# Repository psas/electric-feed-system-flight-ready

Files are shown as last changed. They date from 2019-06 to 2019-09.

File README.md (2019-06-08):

# electric-feed-system-flight-ready

## Introduction

The goal of this project was to develop a cryogenic compatible, flight-ready electric feed system (EFS) for Portland State Aerospace Society for use in their upcoming Launch Vehicle 4 (LV4). This project has made significant advancements in the design and testing of a cryogenic compatible pump. However, more work must be completed before the EFS will be deemed flight-ready. Improvements were made upon previous EFS team’s designs, resulting in a more compact, higher powered, and robust pump system. Crucially, the new design has been tested and confirmed to be cryogenic compatible. The final EFS design has successfully shown PSAS that the pump design is capable of pumping cryogenic fluids without seizing and is able to maintain single-phase fluid flow at the system outlet under specified conditions.

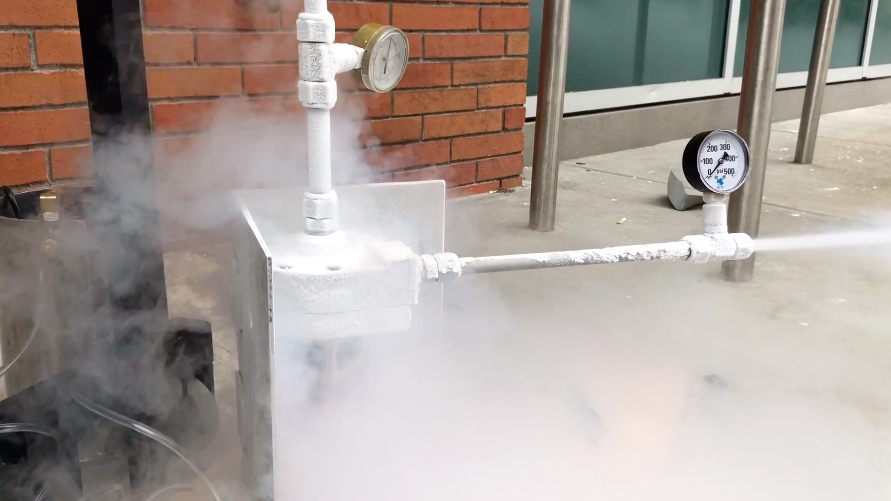
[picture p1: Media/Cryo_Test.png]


## EFS Onboarding

The testing performed on the final cryogenic EFS design for the 2018-2019 PSAS Capstone provided useful knowledge to the organization for continued EFS development. The successful testing of this pump showed that the cryogenic tolerancing functions developed by our team accurately compensate for thermal deformation in the aluminum pump components to allow for proper rotary alignment. Additionally, the cryogenic EFS test showed that this design is capable of pressurizing the cryogenic fluid to obtain single phase fluid flow at the system exit. However, testing has also led to a better understanding of the further work that needs to be performed in order to ready the EFS for flight on LV4. These next steps are outlined below.

### Pump Internals

#### Bearings

The use of a single stainless steel axial thrust roller bearing in the IPA pump displayed inadequate alignment capabilities during this pump's tests. For this reason, the roller bearing was used in conjunction with a Boca ceramic thrust bearing. This resulted in reduced opportunity for misalignment along the rotating element. However, during cryogenic testing, there were several instances of the exit flow momentarily transitioning to gaseous nitrogen at the pump outlet. While the exact cause of this phase duality is not immediately known, one potential source of inconsistency in performance may be from the stainless steel bearing. At cryogenic temperatures, the material of this bearing will contract, which leaves potential for the bearing rollers to rock in the race. For this reason, it is suggested that the second bearing be replaced with either another fully ceramic bearing, or a ceramic-stainless hybrid bearing. This will satisfy the material compatibility of liquid oxygen while ensure optimal performance at cryogenic temperatures.

#### Seals

Testing of the IPA pumps were largely unsuccessful. Misalignment of the rotating element caused the pump to seize during operation. Because the motors selected for the EFS are not rated for high torque applications, this rapid increase in torsional load on the shaft caused the ESC to overload. The likely cause of this was a drastic increase in current as the motor attempted to rotate the pump shaft.

The Flowserve PacSeal used for IPA testing is believed to be, at least in part, the reason for this misalignment. The seal is designed be able to move along the shaft as needed to account for the increase in volute pressure. However, the seal did not perform as designed during testing, and the shaft locked in place.

Additionally, the seal did not adequately retain the fluid as intended. This seal was ultimately selected as a placeholder in the first place, due to it's low cost and ease of accessibility. However, the specifications of this seal do not meet the requirements of the electric feed system in the first place, and as such should not be used in future designs.

For cryogenic testing, the EFS team had to find a sealing solution to meet the upcoming deadline for cryogenic testing. For this reason, a PTFE press-fit sealing collar was developed as a temporary sealing solution. It performed well enough for the purposes of this cryogenic test. However, during this test, gaseous nitrogen leaked from the sealing chamber. For this reason, it is not recommended that this design be considered for future EFS iterations.

Research performed regarding cryogenic dynamic seals with LOX compatibility has led to the selection of a Parker FCC-V spring energized seal (or an equivalent seal from Gallagher Seals) as the optimal seal for both IPA and LOX applications. This selection was identified before cryogenic testing took place. However, due lack of easy access to this seal type, the EFS team was not able to procure seals in time for testing. In the future, it is advised that the next EFS team work on obtaining these seals early on in the development stage.

In order to reduce the total pressure on the seal, it is recommended that the impeller be optimally balanced by adding shallow Barske vanes on the rear face of the impeller in addition to the suction vanes. This helps influence the fluid away from the sealing chamber and back out toward the diffuser, reducing the total pressure the seal experiences.

### Rotary Element Alignment

The sealing and bearing solutions outlined above will help improve alignment in pump shaft rotation. Additionally, a direct motor mount was developed to further decrease variation in alignment. This design improved alignment during cryogenic testing, and is advised to be used in all future designs.

Additionally, it is recommended that the next EFS team consider procuring a motor with an custom extended shaft. With enough length, this shaft can be used to drive the pump directly, removing the need for a coupler. This would reduce the overall size of the system and further improve alignment.

### Instrumentation

While testing of the cryogenic pump was successful and provided results that benefited the development of the PSAS electric feed system, the analog pressure gauges used during the test were not able to operate at such low temperatures. Because of this, no quantitative results were obtained from the test.

Moving forward, it is recommended that further research is performed into cryogenic compatible pressure and flow rate instruments. Ideally, pressure transducers should be integrated into the DAQ system to allow digital conversion of the data. The PSAS Liquid Fuel Engine Test Stand (LFETS) team has performed reasonable amounts of research into both of these instrument types, and their work can be used as a resource for how these measurement devices can best be integrated into the EFS. A LOX compatible differential pressure flowmeter (Venturimeter) is recommended for mass flow data collection. 

### LV4 Integration

#### Test Stand

Future iterations of the EFS pumps should be capable of integrating into the LFETS and used to regulate the pressure and mass flow delivered to the test engine. Once on the test stand, the flow rate and pressure measurements discussed previously will already be measured by the test stand's instrumentation. In this way, both projects will benefit from the work of the other.

#### LV4 Airframe

The current mounting design for both electric feed system pumps consists of the 2 pumps encased in a rectagular mount on opposite corners. This configuration was designed to be compatible with the 12 inch diameter selected for LV4. However, it will be the responsibility of future EFS teams to identify and test the best way to integrate these mounts into the rocket module itself.

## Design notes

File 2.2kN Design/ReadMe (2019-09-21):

Contains calculation tools and Solidworks parts and assemblies for IPA and LOX EFS pumps for use in the 2.2kN LV4 engine.

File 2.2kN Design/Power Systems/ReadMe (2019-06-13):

Block diagrams for EFS overall system and power configuration.

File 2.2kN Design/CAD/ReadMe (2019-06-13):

Solidworks assemblies and parts for IPA and LOX pumps are found in this directory.

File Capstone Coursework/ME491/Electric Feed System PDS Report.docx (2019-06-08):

Product Design Specifications Report

# Flight Ready Electric Feed System

Portland State University

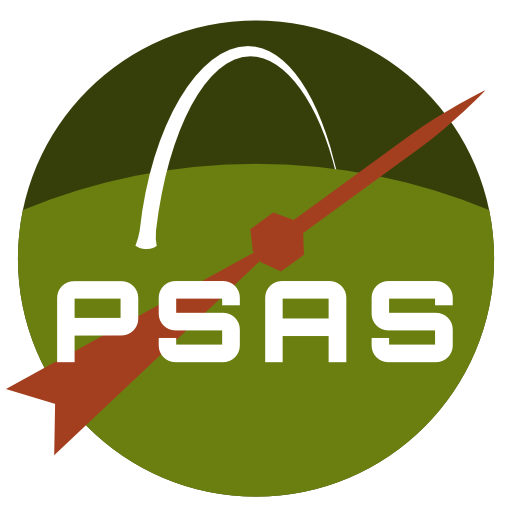
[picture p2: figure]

Group members:

Elrod, Shayli

Garcia, Julio

Ju, Henry

Mendoza, Jonas

Sheldon, Nick

Wahl, Philip

Academic Advisor: Baldur Steingrimsson

Sponsor: Portland State Aerospace Society

DOCUMENT CONTENTS

INTRODUCTION 2

MISSION STATEMENT 2

PROJECT PLAN (Top-Level) 3

CUSTOMER IDENTIFICATION 5

CUSTOMER FEEDBACK 5

PDS 6

CONCLUSIONS 8

ATTACHMENTS 8

### INTRODUCTION

Portland State Aerospace Society (PSAS) requires the production of a device that can be used to increase fluid pressures in both the Liquid Fuel Engine Test Stand (LFETS) and PSAS liquid fuel rockets in flight. The Flight Ready Electric Feed System (EFS) is an electronically controlled pump system to be designed for the Launch Vehicle 4 (LV4). This project has been proposed by PSAS in order to make the use of lightweight, low-pressure composite propellent flight tanks possible. As opposed to utilizing a more traditional high pressure 'blow down" system, an EFS will be used to provide the necessary pressure to pump the propellants into the engine. Design and manufacturing of the EFS will be a part of a senior capstone project involving six Mechanical Engineering students. This approachable and affordable alternative to a pressurized tank is a challenging and innovative task for an amateur rocket design.

### MISSION STATEMENT

“To provide affordable, lightweight propulsion system technology increasing the capabilities of amatuer rocketry and student education.”

### PROJECT PLAN (Top-Level)

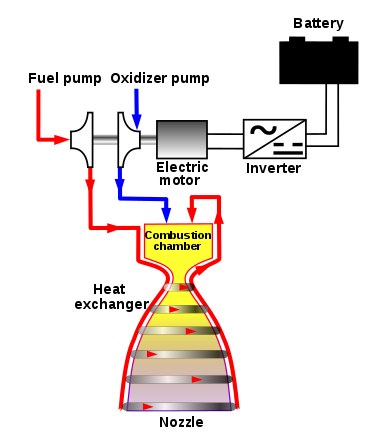
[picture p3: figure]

The pump design will utilize electric drive shafts to introduce mechanical work into the system in order to produce a pressure increase. Each housing will be optimized for the required pressure of two independent fluids. The pump design will be optimized for flight capability, utilizing a compact lightweight casing to enclose individual chambers which separately increase the pressure of Isopropyl Alcohol and Liquid Oxygen. The pump will be powered by an onboard Lithium Ion battery pack, providing DC current to an electric inverter. AC converted current will power the brushless motors to provide shaft power in order to rotate off the impellers within the system. As the system provides rotational energy, the pressure of the incoming propellants will increase from 45 PSI to 500 PSI as the impellers increase the propellant potential energy.

The manufacturing process will begin with 3D rendering in SolidWorks to create the shape and layout of the housings and motors. A machinable prototype needs to fit within specified dimensions of the airframe module which will house the onboard EFS. A functional design will be followed by ANSYS vibrational and thermal analysis to show evidence of structural integrity. Once the design has been analytically verified, it will be approved and passed on to the CNC machine shop for physical fabrication. Initial machine prototypes will be machined out of inexpensive plastics for trial mock-ups before any machining out of metal will begin.

The corrosive properties of liquid oxygen will limit the material options for pump component which will come into contact with it. 304 Stainless steel is the most common metal alloy used for liquid oxygen components, and its availability makes it a logical candidate for material selection. In addition, research will be performed on the feasibility of using alternative materials that may be more cost effective and easier to machine, such as aluminum alloys.

Tolerance testing will begin upon completion of machined parts in either plastic or metal. All dimensions will be compared against the CAD model for machining accuracy and precision. Once a metal casing has been created leak testing will check for fitment of the final assembly. The pump will be assembled and then filled with water, up to 1000 psi, to search for any leaks in the system. Continued system testing will research durability against vibrational and acceleration force as the pump will be subjected to a harsh launch environment. It is imperative that the system is not compromised so the rocket can achieve consistent thrust during flight.

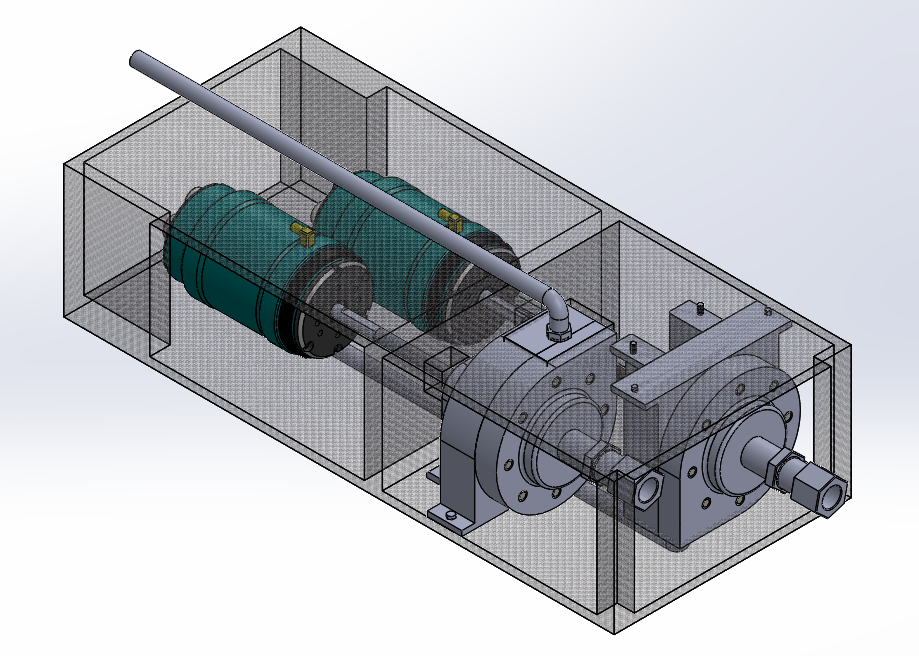
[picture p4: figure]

Upon completion, the desired deliverable is a tested electronically controlled pump that is suitable for successful use during flight. Crucially, the pump and associated system components must be compatible both propellants and ensure absolute fluid separation at all points within the system. Cross-contamination of fluids will be considered a design failure and impose a major safety risk. The minimum lifespan without significant overhaul is ten full-length engine test fires. Surpassing ten fires is preferred if at all possible. The pump and its related systems should be embedded with sensors for required data collection, as this testing data is also a deliverable. The milestone timeline for the project can be seen in Table 2 (see attachments).

### CUSTOMER IDENTIFICATION

Portland State Aerospace Society will be sponsoring this capstone project and is responsible for all the given requirements. In addition, the Oregon NASA Space Grant Consortium (OSGC) will also be sponsoring our Flight Ready EFS capstone after winning an Undergraduate Team Experience Award Program grant. This additional sponsor will add extra requirements to be fulfilled by the capstone team such as a project presentation to the OSGC board as publishing project documentation. The requirements from both customers are outlined in Table 3 (see attachments).

### CUSTOMER FEEDBACK

The Flight Ready EFS Capstone group will provide a weekly update to PSAS through a short presentation at the general meetings. This will ensure all progress is shared with the customer and all designs are to be to review as they progress. Use of funds will involve direct communication with OSGC on a per part basis. All purchase requests will be review by the team’s Principal Investigator and then sent off to OSGC for reimbursement. All declined part requests will undergo a secondary review in order to reselect a similar part which can be purchased.

### PRODUCT DESIGN SPECIFICATION (PDS)

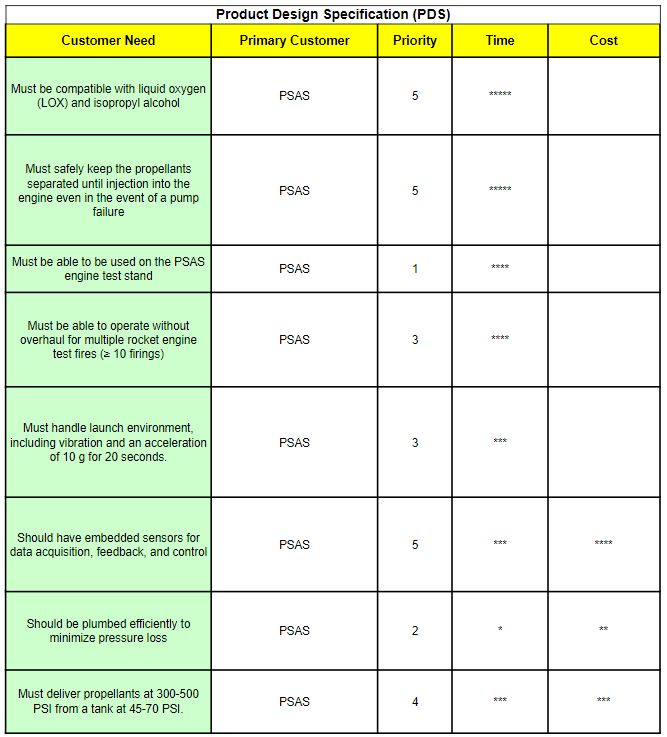
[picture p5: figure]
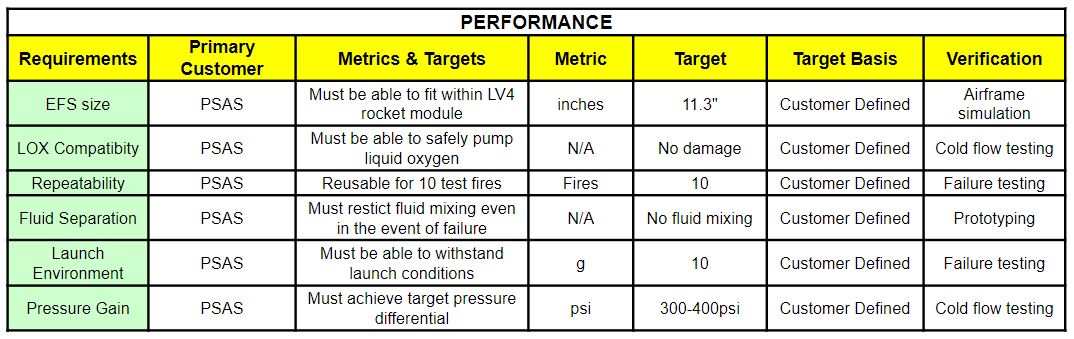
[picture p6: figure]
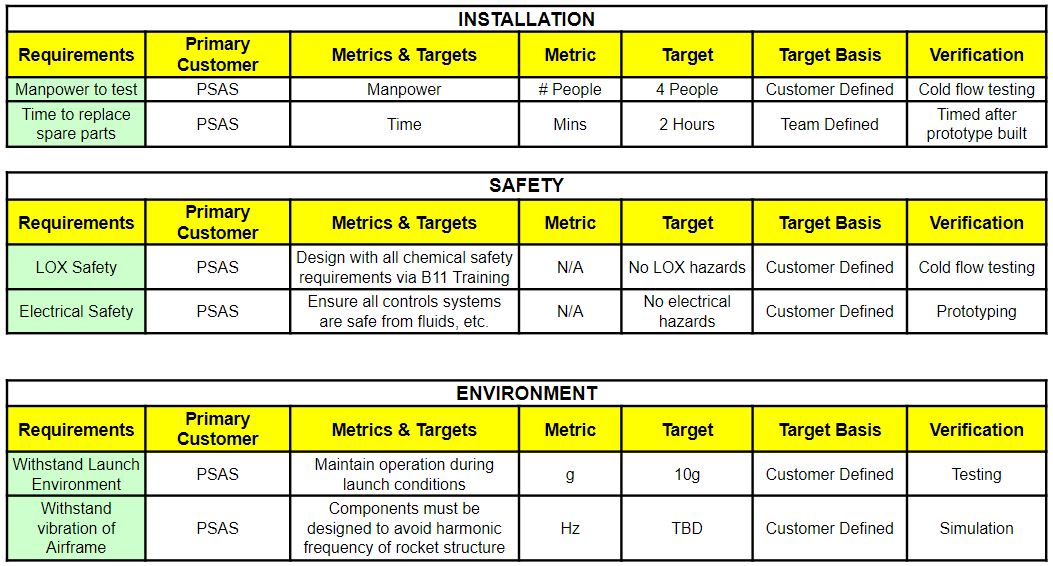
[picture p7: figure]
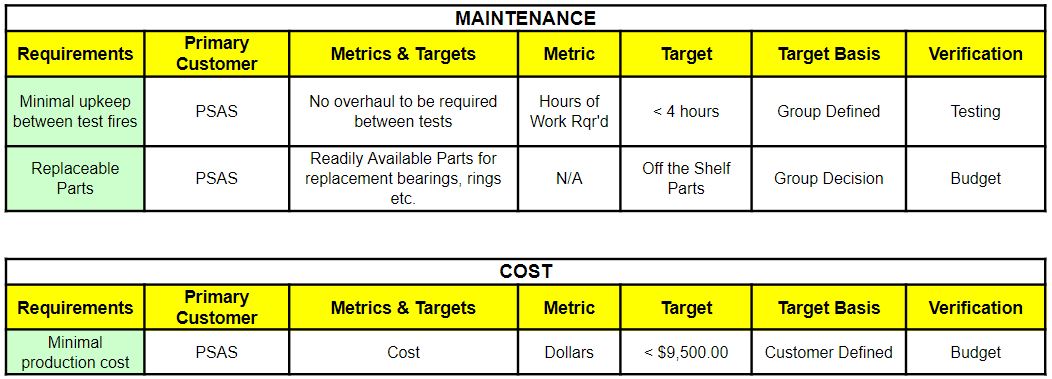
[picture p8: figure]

### CONCLUSIONS

The Flight Ready Electric Feed System, upon completion, will be a major accomplishment for the amateur aerospace community. This project will further develop research performed by previous and concurrent PSU Capstone teams associated with the liquid propulsion team within PSAS. Over the next few months, we anticipate developing a cryogenic, electronically controlled, propellant delivery system for Launch Vehicle 4 as specified by our Capstone Sponsor, PSAS. By the end of the school year will be presenting our findings, prototype, and publish all documentation related to the project.

### ATTACHMENTS

Table 1: Electric Feed System Project Budget

Item | Description | Vendor | Award Amount | 1.5:1 Cost Share

Cost Share
In-Kind AY effort | Dr. Mark Weislogel donating his time working as PI on Project | Portland State University | | $6,556

Award Budget
304 SS Steel | The raw material used to machine pump housing | McMaster-Carr | $800
Tooling | Pump House machine tooling | Western Precision Products Inc | $1,400
6061 Aluminum | Raw Material to create EFS Airframe Structure | McMaster-Carr | $200
304 SS Steel | ¼” x 24” TGP Precision Shaft | Metals Depot | $10
Impeller | Rotational Impellers for propellants | Shapeways | $200
ISO Plumbing | Various plumbing fittings for alcohol | Home Depot | $100
LOX Plumbing | Various LOX compatible fittings | AcmeCryo | $300
Aluminum Piping | ½” Aluminum piping for plumbing | Metals Depot | $100
Seals | Metal C-Ring Internal Pressure Face Seals | Parker | $30
Liquid Oxygen | 40 Gallons of LOX for testing | Airgas | $200
Liquid Nitrogen | 40 Gallons of LN for cryo testing | Airgas | $200
Electric Motor | Brushless Motor for shaft drive | Hobbyking | $150
Heat Sink | Heat Sink for Brushless motor | Amazon | $25
Arduino | Arduino to Controlling pump | Amazon | $50
Sensing Equipment | Pressure Transducers and flow meters for fluid monitoring | Omega | $500
Total Direct Costs | | | $4,265 | $6,556
Total Indirect Costs | | 48.50% | $2,069 | $3,180
Total Project Costs | | | $6,334 | $9,736
Cost Share Ratio | 1.537

Table 2: EFS Completion Timeline

Week | Milestone Description
1 - 3 | Research and locate budget line items to optimize spending. Discus pump design process to dictate the purchase sequence.
4 - 6 | Finalize design for preliminary prototyping with 3D printing and mock testing
7 - 10 | Integrate Control system with proven test design
11 - 15 | Coordinate Electric Feed System design with Engine Test Stand and Airframe
16 - 20 | Begin manufacturing process for steel housing, plumbing, and airframe fixture
21 - 22 | Testing cryogenic compatibility, fluid leak, and durability to cycle usage
23 - 25 | Department testing with Test Stand and Airframe
26 - 27 | Finalize Electric Feed System Design
28 - 30 | Organize project material for finalized report and presentation

Table 3: Customer Requirements for PSAS and OSGC

PSAS Requirements | NASA OSGC Requirements
Must be compatible with liquid oxygen (LOX) and isopropyl alcohol | Citation of OSGC as a source of funding in all publications
Must safely keep the propellants separated until injection into the engine even in the event of a pump failure | Complete list of resulting publications
Must be able to be used on the PSAS engine test stand | Final budget
Must be able to operate without overhaul for multiple rocket engine test fires (≥ 10 firings) | Report on project outcome
Must handle the launch environment, including vibration and an acceleration of 10 g for 20 seconds. | Presentation of results at the OSGC Student Symposium in (Nov 2019)
Should have embedded sensors for data acquisition, feedback, and control
Should be plumbed efficiently to minimize pressure loss
Must deliver propellants at 300-500 PSI from a tank at 45-70 PSI.

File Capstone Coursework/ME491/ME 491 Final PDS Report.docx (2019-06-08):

ME 491 | Fall 2018

Product Design Specifications Report

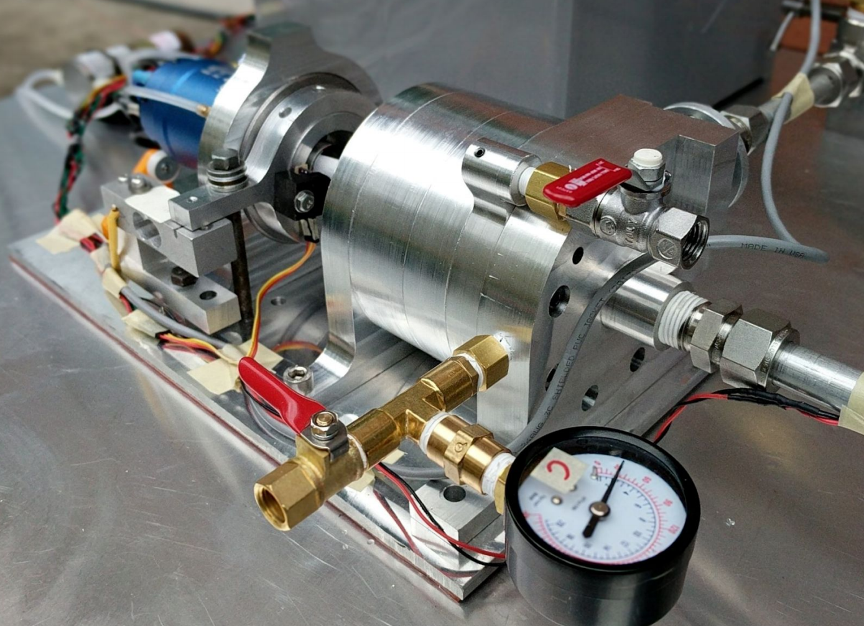
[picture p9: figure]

Flight Ready

Electric Feed System

TEAM MEMBERS:

Julio Garcia

Philip Wahl

Jonas Mendoza

Nick Sheldon

Henry Ju

Shayli Elrod

ACADEMIC ADVISOR:

Baldur Steingrimsson

Sponsored by Portland State Aerospace Society (PSAS)

DOCUMENT CONTENTS

INTRODUCTION 3 (https://docs.google.com/document/d/1pQuV71Iw2FOw1OESzgzDGfmaMRiZPIVxerrv7SGsqSI/edit)

MISSION STATEMENT 3 (https://docs.google.com/document/d/1pQuV71Iw2FOw1OESzgzDGfmaMRiZPIVxerrv7SGsqSI/edit)

PROJECT PLAN (Top-Level) 4-5 (https://docs.google.com/document/d/1pQuV71Iw2FOw1OESzgzDGfmaMRiZPIVxerrv7SGsqSI/edit)

CUSTOMER IDENTIFICATION (https://docs.google.com/document/d/1pQuV71Iw2FOw1OESzgzDGfmaMRiZPIVxerrv7SGsqSI/edit) 6

CUSTOMER FEEDBACK (https://docs.google.com/document/d/1pQuV71Iw2FOw1OESzgzDGfmaMRiZPIVxerrv7SGsqSI/edit) 6

PDS (https://docs.google.com/document/d/1pQuV71Iw2FOw1OESzgzDGfmaMRiZPIVxerrv7SGsqSI/edit) 7-8

CONCLUSIONS (https://docs.google.com/document/d/1pQuV71Iw2FOw1OESzgzDGfmaMRiZPIVxerrv7SGsqSI/edit) 9

ATTACHMENTS (https://docs.google.com/document/d/1pQuV71Iw2FOw1OESzgzDGfmaMRiZPIVxerrv7SGsqSI/edit) 10-12

INTRODUCTION

Portland State Aerospace Society (PSAS) requires the production of a flight ready device that can be used to increase fluid pressure in both the Liquid Fuel Engine Test Stand (LFETS) and PSAS liquid fuel rocket. The Flight Ready Electric Feed System (EFS) is an electronically controlled pump system to be designed for the Launch Vehicle 4 (LV4). This project has been proposed by PSAS in order to make the use of lightweight, low-pressure, composite propellent flight tanks possible. As opposed to utilizing a more traditional high pressure 'blow down" system, an EFS will be used to provide the necessary pressure to pump the propellants into the engine. Design and manufacturing of the EFS will be a part of a senior capstone project involving six Mechanical Engineering students. This approachable and affordable alternative to a pressurized tank is a challenging and innovative task for an amateur rocket design.

MISSION STATEMENT

“To provide an affordable, lightweight propulsion system technology increasing the capabilities of amateur rocketry and student education.”

PROJECT PLAN (Top-Level)

The pump design will utilize electric drive shafts to introduce mechanical work into the system in order to produce an increase in pressure. Each housing will be optimized for the required pressure of two independent fluids. The pump design will be designed for flight capability, utilizing a compact lightweight casing to enclose individual chambers which separately increase the pressure of isopropyl alcohol and liquid oxygen (Figure 1). The pump will be powered by an onboard lithium ion battery pack, providing DC current to an electric inverter. AC converted current will power the brushless motors to provide shaft power in order to rotate off the impellers within the system. As the system provides rotational energy, the pressure of the incoming propellants will increase from 45 PSI to 500 PSI as the impellers increase the propellant potential energy.

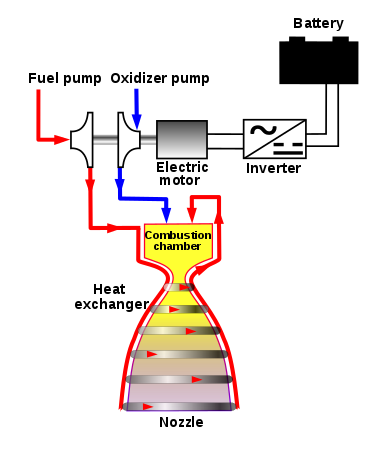
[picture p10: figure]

Figure : Overview of EFS System

The manufacturing process will begin with 3D rendering in SolidWorks to create the shape and layout of the housing and motors. A machinable prototype needs to fit within specified dimensions of the airframe module which will house the onboard EFS. A functional design will be followed by ANSYS vibrational and thermal analysis to show evidence of structural integrity. Once the design has been analytically verified, it will be approved and passed on to the CNC machine shop for physical fabrication. Initial machine prototypes will be machined out of inexpensive plastics for trial mock-ups before any machining out of metal will begin.

The corrosive properties of liquid oxygen will limit the material options available for pump components that will come into contact with it. 304 stainless steel is the most common metal alloy used for liquid oxygen components and its availability makes it a logical candidate for material selection. In addition, research will be performed on the feasibility of using alternative materials that may be more cost effective and easier to machine, such as aluminum alloys.

Tolerance testing will begin upon completion of machined parts in either plastic or metal. All dimensions will be compared against the CAD model for machining accuracy and precision. Once a metal casing has been created leak testing will check for fitment of the final assembly. The pump will be assembled and then filled with water (up to 1000 psi) to search for any leaks in the system. Continued system testing will research durability against vibrational and acceleration force as the pump will be subjected to a harsh launch environment. It is imperative that the system is not compromised so the rocket can achieve consistent thrust during flight.

Upon completion, the desired deliverable is a tested electronically controlled pump that is suitable for successful use during flight. Crucially, the pump and associated system components must be compatible with both propellants and ensure absolute fluid separation at all points within the system. Cross-contamination of fluids will be considered a design failure and impose a major safety risk. The minimum lifespan without significant overhaul is ten full-length engine test fires. Surpassing ten fires is preferred if possible. The pump and its related systems should be embedded with sensors as this testing data is also a required deliverable. The milestone timeline for the project can be seen in Table 2 (see attachments).

CUSTOMER IDENTIFICATION

Portland State Aerospace Society will be sponsoring this capstone project and is responsible for all the given requirements. In addition, the Oregon NASA Space Grant Consortium (OSGC) will also be sponsoring our Flight Ready EFS capstone after winning an Undergraduate Team Experience Award Program grant. This additional sponsor will add extra requirements to be fulfilled by the capstone team such as a project presentation to the OSGC board as publishing project documentation. The requirements from both customers are outlined in Table 3 (see attachments).

CUSTOMER FEEDBACK

The Flight Ready EFS Capstone group will provide a weekly update to PSAS through a short presentation at the general meetings. This will ensure all progress is shared with the customer and all designs are to be to review as they progress. Use of funds will involve direct communication with OSGC on a per part basis. All purchase requests will be review by the team’s Principal Investigator and then sent off to OSGC for reimbursement. All declined part requests will undergo a secondary review in order to reselect a similar part which can be purchased.

PRODUCT DESIGN SPECIFICATION (PDS)

Table 1: Customer Requirements

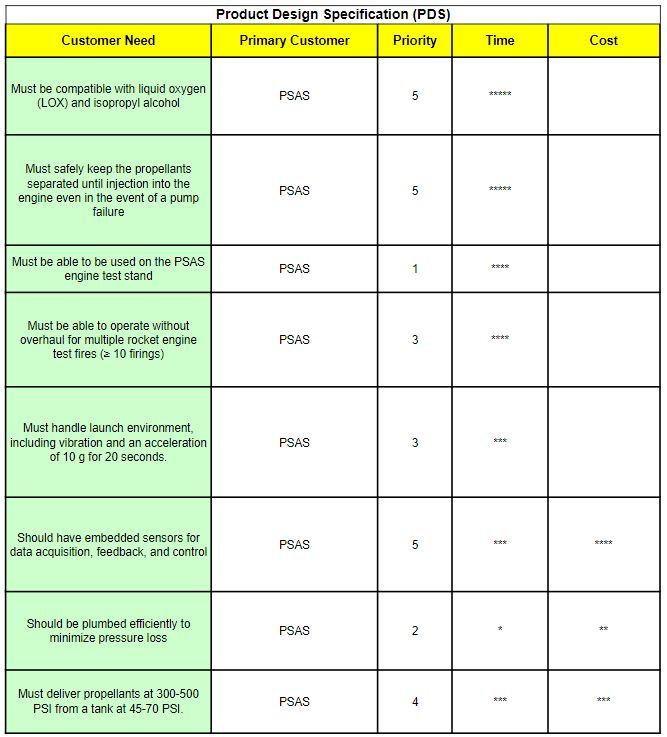
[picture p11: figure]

PRODUCT DESIGN SPECIFICATION (PDS)

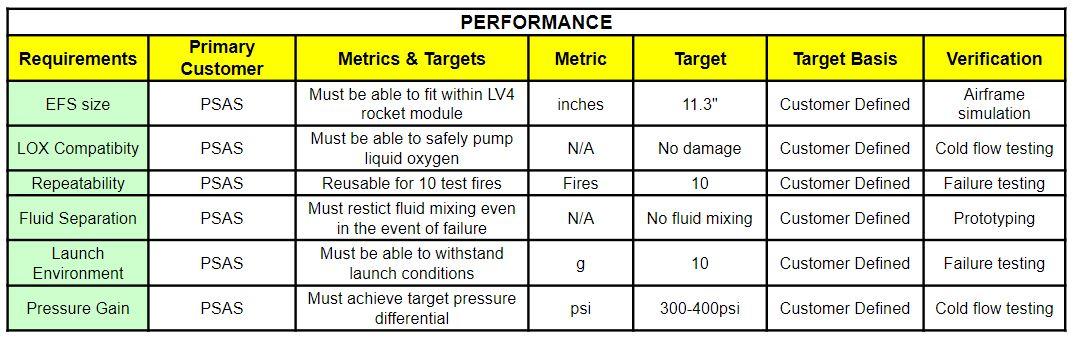
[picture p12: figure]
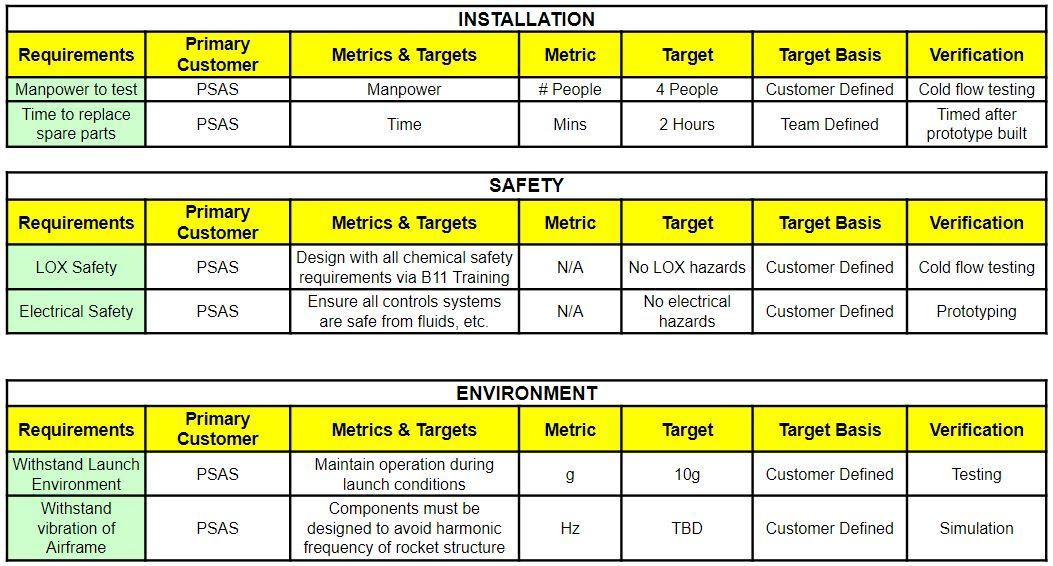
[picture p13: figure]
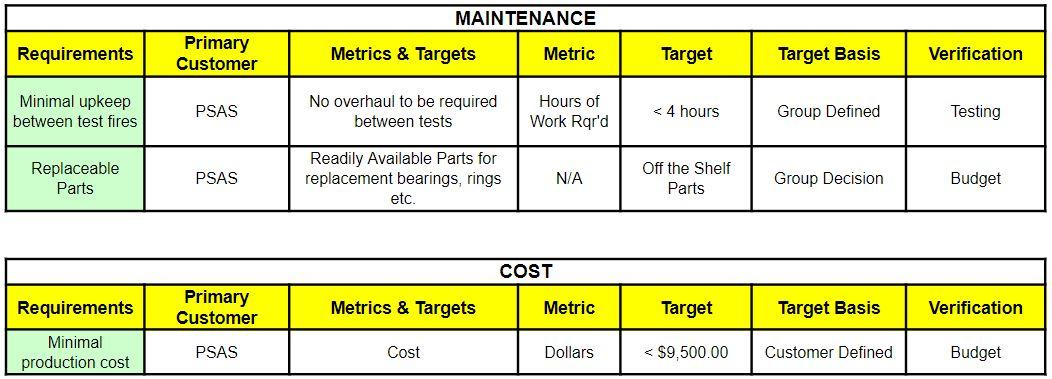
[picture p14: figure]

CONCLUSIONS

The Flight Ready Electric Feed System upon completion, will be a major accomplishment for the amateur aerospace community. This project will further develop research performed by previous and concurrent PSU Capstone teams associated with the liquid propulsion team within PSAS. Over the next few months, we anticipate developing a cryogenic, electronically controlled, propellant delivery system for Launch Vehicle 4 as specified by our Capstone Sponsor, PSAS. By the end of the school year, we will be presenting our findings, prototype, and will publish all documentation related to the project.

ATTACHMENTS

Table 1: Electric Feed System Project Budget

Item | Description | Vendor | Award Amount | 1.5:1 Cost Share

Cost Share
In-Kind AY effort | Dr. Mark Weislogel donating his time working as PI on Project | Portland State University | | $6,556

Award Budget
304 SS Steel | The raw material used to machine pump housing | McMaster-Carr | $800
Tooling | Pump House machine tooling | Western Precision Products Inc | $1,400
6061 Aluminum | Raw Material to create EFS Airframe Structure | McMaster-Carr | $200
304 SS Steel | ¼” x 24” TGP Precision Shaft | Metals Depot | $10
Impeller | Rotational Impellers for propellants | Shapeways | $200
ISO Plumbing | Various plumbing fittings for alcohol | Home Depot | $100
LOX Plumbing | Various LOX compatible fittings | AcmeCryo | $300
Aluminum Piping | ½” Aluminum piping for plumbing | Metals Depot | $100
Seals | Metal C-Ring Internal Pressure Face Seals | Parker | $30
Liquid Oxygen | 40 Gallons of LOX for testing | Airgas | $200
Liquid Nitrogen | 40 Gallons of LN for cryo testing | Airgas | $200
Electric Motor | Brushless Motor for shaft drive | Hobbyking | $150
Heat Sink | Heat Sink for Brushless motor | Amazon | $25
Arduino | Arduino to Controlling pump | Amazon | $50
Sensing Equipment | Pressure Transducers and flow meters for fluid monitoring | Omega | $500
Total Direct Costs | | | $4,265 | $6,556
Total Indirect Costs | | 48.50% | $2,069 | $3,180
Total Project Costs | | | $6,334 | $9,736
Cost Share Ratio | 1.537

Table 2: EFS Completion Timeline

Week | Milestone Description
1 - 3 | Research and locate budget line items to optimize spending. Discus pump design process to dictate the purchase sequence.
4 - 6 | Finalize design for preliminary prototyping with 3D printing and mock testing
7 - 10 | Integrate Control system with proven test design
11 - 15 | Coordinate Electric Feed System design with Engine Test Stand and Airframe
16 - 20 | Begin manufacturing process for steel housing, plumbing, and airframe fixture
21 - 22 | Testing cryogenic compatibility, fluid leak, and durability to cycle usage
23 - 25 | Department testing with Test Stand and Airframe
26 - 27 | Finalize Electric Feed System Design
28 - 30 | Organize project material for finalized report and presentation

Table 3: Customer Requirements for PSAS and OSGC

PSAS Requirements | NASA OSGC Requirements
Must be compatible with liquid oxygen (LOX) and isopropyl alcohol | Citation of OSGC as a source of funding in all publications
Must safely keep the propellants separated until injection into the engine even in the event of a pump failure | Complete list of resulting publications
Must be able to be used on the PSAS engine test stand | Final budget
Must be able to operate without overhaul for multiple rocket engine test fires (≥ 10 firings) | Report on project outcome
Must handle the launch environment, including vibration and an acceleration of 10 g for 20 seconds. | Presentation of results at the OSGC Student Symposium in (Nov 2019)
Should have embedded sensors for data acquisition, feedback, and control
Should be plumbed efficiently to minimize pressure loss
Must deliver propellants at 300-500 PSI from a tank at 45-70 PSI.

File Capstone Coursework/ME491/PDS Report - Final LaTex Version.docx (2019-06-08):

ME 491 | Fall 2018 Product Design Specifications Report

TO

CHILLE PUS

Flight Ready Electric Feed System

TEAM MEMBERS: Julio Garcia Philip Wahl Jonas Mendoza Nick Sheldon Henry Ju Shayli Elrod

Sponsored by Portland State Aerospace Society (PSAS)

ACADEMIC ADVISOR: Baldur Steingrimsson

DOCUMENT CONTENTS

INTRODUCTION

MISSION STATEMENT

PROJECT PLAN (Top-Level)

CUSTOMER IDENTIFICATION

CUSTOMER FEEDBACK

PDS

CONCLUSIONS

ATTACHMENTS

INTRODUCTION

Portland State Aerospace Society (PSAS) requires the production of a flight ready device that can be used to increase fluid pressure in both the Liquid Fuel Engine Test Stand (LFETS) and PSAS liquid fuel rocket. The Flight Ready Electric Feed System (EFS) is an electronically controlled pump system to be designed for the Launch Vehicle 4 (LV4). This project has been proposed by PSAS in order to make the use of lightweight, low-pressure, composite propellent flight tanks possible. As opposed to utilizing a more traditional high pressure "blow down” system, an EFS will be used to provide the necessary pressure to pump

the propellants into the engine. Design and manufacturing of the EFS will be a part of a

senior capstone project involving six Mechanical Engineering students. This approachable

and affordable alternative to a pressurized tank is a challenging and innovative task for an

amateur rocket design.

MISSION STATEMENT

“To create affordable, lightweight rocket propulsion technology that will increase the

capabilities of amateur rocketry and student education.”

PROJECT PLAN (Top-Level)

ESSIN

The pump design will utilize electric drive shafts to introduce mechanical work into the system, producing an increase in pressure. Each housing will be optimized for the required pressure of two independent fluids. The pump design will be designed for flight capability, utilizing a compact lightweight casing to enclose individual chambers which separately in crease the pressure of isopropyl alcohol and liquid oxygen. The pump will be powered by an onboard lithium ion battery pack, providing DC current to an electric inverter. AC converted

current will power the brushless motors to provide shaft power in order to rotate both of the specially engineered pumps within the system as shown in Figure 1. As the system provides rotational energy, the pressure of the incoming propellants will increase from 45 PSI to 500 PSI as the impellers increase the propellant potential energy.

er

a

Battery

Fuel pump Oxidizer pump

erter

Electric motor

The manufacturing process will begin with 3D rendering in SolidWorks to create the shape and layout of the housing and motors. A machinable prototype needs to fit within specified dimensions of the airframe module which will house the onboard EFS. A func tional design will be followed by ANSYS vi brational and thermal analysis to show ev idence of structural integrity. Once the de sign has been analytically verified, it will be approved and passed on to the CNC ma chine shop for physical fabrication. Initial machine prototypes will be machined out of inexpensive plastics for trial mock-ups be fore any machining out of metal will begin.

Combus lon chamber

Heat exchanger

Nozzle

e

Figure 1: Overview of an EFS

The corrosive properties of liquid oxygen will

mmon

limit the material options available for pump components that will come into contact with it. 304 stainless steel is the most common metal alloy used for liquid oxygen components and its availability makes it a logical candidate for material selection. In addition, research will be performed on the feasibility of using alternative materials that may be more cost effective and easier to machine, such as aluminum alloys. Table 6: Electric Feed System

Project Budget summarizes our expected component costs and plan to stay within the given customer budget (see attachments).

Tolerance testing will begin upon completion of machined parts in either plastic or metal. All dimensions will be compared against the CAD model for machining accuracy and precision. Once a metal casing has been created leak testing will check for fitment of the final assembly. The pump will be assembled and filled with water (up to 1000 psi) to identify any potential leakage points in the system. In addition, we will analyze the resilience of the system from vibration effects, as well as the effects of gravitational force, as the pump will be subjected to a harsh launch environment. It is imperative that the system is not compromised so the rocket can achieve consistent thrust during flight.

manc

Upon completion, the desired deliverable is a tested electronically controlled pump that provides reliable performance during flight. Crucially, the pump and associated system components must be compatible with both propellants and ensure absolute fluid separation at all points within the system. Cross-contamination of fluids will be considered a design failure and impose a major safety risk. The minimum lifespan without significant overhaul is

ten full-length engine test fires. Surpassing ten fires is preferred if possible. The pump and its related systems should be embedded with sensors as this testing data is also a required deliverable. The milestone timeline for the project can be found in Table 4: EFS Completion

Timeline (see attachments).

2TSOTS

CUSTOMER IDENTIFICATION

en

Sum

ma

ler 1

DIT

Portland State Aerospace Society will be sponsoring this capstone project and is responsible for all of the given engineering requirements. Table 1: Product Design Specifications sum marizes the customer needs and their ranking of priority upon final completion. Further, Table 2: Customer Requirements, and Table 3: Engineering Requirements, cover targets and metrics as well as the verification process for achieving these goals. In addition, the Oregon NASA Space Grant Consortium (OSGC) will also be sponsoring the Flight Ready EFS cap

stone, as the project proposal has won an Undergraduate Team Experience Award Program (UTEAP) grant. Upon acceptance of the grant, OSGC has required the project team to raise a non-negotiable amount of 1.5 times the donation through fundraising or further faculty donation of advisory time. Dr. Mark Weislogel has agreed to work as the faculty advisor to meet this requirement. His cost share portion donation can also be found in Table 6. This additional sponsor will require a project presentation to the OSGC board to serve as publish ing project documentation. The basic level requirements from both customers are outlined in Table 5: Customer Requirements For PSAS and Oregon Space Grant Consortium.

CUSTOMER FEEDBACK

The Flight Ready EFS Capstone group will provide a weekly update to PSAS through a short presentation at the general meetings. This will ensure all progress is shared with the customer and all designs are to be to reviewed as they progress. Use of funds will involve direct communication with OSGC on a per part basis. All purchase requests will be reviewed by the teams Principal Investigator and then sent off to OSGC for reimbursement. All declined part requests will undergo a secondary review in order to reselect a similar part

which can be purchased.

PRODUCT DESIGN SPECIFICATION (PDS)

The PDS tables below will serve as a resource to structure the EFS design agenda over the next coming months. Numerical target values and item priority will make for simplified task assignment amongst team members, as well as, communication reference when reporting progress and results to PSAS and OSGC.

Table 1: Product Design Specification

Product Design Specification (PDS)

Custom er Need

Primary Customer

Priority

Time

Must be compatible with liquid oxygen

(LOX) and isopropyl alcohol

PSAS

Must safely keep the propellants separated until injection into the engine

even in the event of a pump failure

PSAS

tttt

Must be able to be used on the PSAS

engine test stand

tttt

PSAS

Must be able to operate without overhaul for multiple rocket engine test

fires > 10 firings)

*

**

PSAS

Must handle launch environment, including vibration and an acceleration

of 10 g for 20 seconds.

PSAS

Should have embedded sensors for data acquisition, feedback, and control

PSAS

Should be plumbed efficiently to

minimize pressure loss

PSAS

Must deliver propellants at 300-500

PSI from a tank at 45-70 PSI.

PSAS

Table 2: Customer Requirements

Customer Requirements

Requirements

Primary Customer

Metrics & Targets

Metric

Target

Target Basis

Verification

LOX Compatibity

PSAS

| Must be able to safely pump

liquid oxygen

NIA

No damage

Customer Defined

Cold flow testing

Performance

Fluid Separation

PSAS

Must restict fluid mixing even in

the event of failure

N/A

No fluid mixing

Customer Defined

Prototyping

Manpower to test

PSAS

Manpower

# People

I

4 People

Customer Defined

Cold flow testing

Installation

Time to replace

spare parts

PSAS

Time

Mins

2 Hours

Team Defined

Timed after prototype built

LOX Safety

PSAS

Design with all chemical safety requirements via B11 Training

N/A

No LOX hazards

Customer Defined

Cold flow testing

Safety

Electrical Safety

PSAS

N/A

No electrical

hazards

Customer Defined

Prototyping

Ensure all controls systems

are safe from fluids, etc. No overhaul to be required

between tests

Minimal upkeep between test fires

PSAS

Hours of Work Ror'd

<4 hours

Group Defined

Testing

Cost Maintenance

Replaceable Parts

PSAS

Readily Available Parts for replacement bearings, rings etc.

N/A

Off the Shelf

Parts

Group Decision

Budget

Minimal production cost

PSAS

Cost

Dollars

< $9,500.00

Customer Defined

Budget

Table 3: Engineering Requirements

Engineering Requirements

Requirements

Primary Customer

Metrics & Targets

Metric

Target Basis

Verification

EFS size

PSAS

Must be able to fit within LV4

rocket module

inches

11.3"

Customer Defined | Airframe simulation

Repeatability

PSAS

Reusable for 10 test fires

# Fires

10

Customer Defined

Failure testing

Performance

Launch Environment

PSAS

10

Customer Defined

Failure testing

Pressure Gain

PSAS

300-400psi

Customer Defined

Cold flow testing

PSAS

Must be able to withstand

launch conditions Must achieve target pressure

differential Maintain operation during

launch conditions Components must be designed to avoid harmonic frequency of

rocket structure

10g

Customer Defined

Testing

Environment

Withstand Launch

Environment Withstand vibration of

Airframe

PSAS

TBD

Customer Defined

Simulation

CONCLUSIONS

Con

The Flight Ready Electric Feed System, upon completion, will be a major accomplishment for the amateur aerospace community. This project will further develop research performed by previous and concurrent PSU Capstone teams associated with the liquid propulsion team within PSAS. Over the next few months, we anticipate developing a cryogenic, electronically controlled, propellant delivery system for Launch Vehicle 4 as specified by our Capstone Sponsor, PSAS. By the end of the school year, we will be presenting our findings, prototype, and will publish all documentation related to the project.

8

ATTACHMENTS

Table 4: Electric Feed System Milestone Timeline

Week Milestone Description

1-3

Research and locate budget line items to optimize spending. Discus pump design process to dictate the purchase sequence.

4-6

Finalize design for preliminary prototyping with 3D printing and mock testing

7-10

Integrate Control system with proven test design

Coordinate Electric Feed System design with Engine Test Stand and Airframe

15

16 - 20

Begin manufacturing process for steel housing, plumbing, and airframe fixture

21.

Testing cryogenic compatibility, fluid leak, and durability to cycle usage

22

23 - 25

Department testing with Test Stand and Airframe

Finalize Electric Feed System Design

26 - 27

28 - 30

Organize project material for finalized report and presentation

Table 5: Customer Requirements For PSAS and Oregon Space Grant Consortium

Week

Milestone Description

1-3

Research and locate budget line items to optimize spending. Discus pump design process to dictate the purchase sequence.

4-6

Finalize design for preliminary prototyping with 3D printing and mock testing

7 - 10

Integrate Control system with proven test design

Coordinate Electric Feed System design with Engine Test Stand and Airframe

11 - 15

16 - 20

Begin manufacturing process for steel housing, plumbing, and airframe fixture

21 -

Testing cryogenic compatibility, fluid leak, and durability to cycle usage

22

23 - 25

Department testing with Test Stand and Airframe

26 - 27

Finalize Electric Feed System Design

| 28 - 30

Organize project material for finalized report and presentation

10

Table 6: Electric Feed System Project Budget

Item

Description

Vendor

Award Amount

1.5:1 Cost

Share

Cost Share

In-Kind AY effort

$6,556

Dr. Mark Weislogel donating his time Portland State working as PI on Project

University

Award Budget The raw material used to machine pump

McMaster-Car housing

304 SS Steel

$800

Tooling

Pump House machine tooling

Western Precision Products Inc

$1,400

6061 Aluminum

Raw Material to create EFS Airframe

Structure

McMaster-Cart

$200

304 SS Steel

44" x 24" TGP Precision Shaft

Metals Depot

$10

Impeller

Rotational Impellers for propellants

Shapeways

$200

ISO Plumbing

Various plumbing fittings for alcohol

Home Depot

$100

Various LOX compatible fittings

AcmeCryo

$300

LOX Plumbing

Aluminium Piping Seals

* Aluminum piping for plumbing

Metals Depot

$100

Metal C-Ring Internal Pressure Face Seals Parker

$30

Liquid Oxygen

40 Gallons of LOX for testing

Airgas

$200

Liquid Nitrogen 40 Gallons of LN for cryo testing

Airgas

$200

Electric Motor

Brushless Motor for shaft drive

Hobbyking

Heat Sink

Heat Sink for Brushless motor

Amazon

$150 $25

$50

Arduino

Amazon

Arduino to Controlling pump Pressure Transducers and flow meters for fluid monitoring

Omega

$500

Sensing Equipment Total Direct Costs

$4,265

$6,556

Total Indirect Costs

48.50%|

$2,069

$3,180

Total Project Costs

$6,334

$9,736

Cost Share Ratio

1.591

1.537

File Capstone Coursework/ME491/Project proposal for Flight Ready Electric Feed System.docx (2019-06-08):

# Project title: Flight ready Electric Feed System

A 2018-2019 MME capstone project sponsored by the Portland State Aerospace Society

## Sponsor contact information

Andrew Greenberg Joe Shields

503-708-7711 971-226-9393

adg@ece.pdx.edu shields6@pdx.edu

## Project motivation

PSAS is using low pressure composite propellant tanks in its first liquid fuel rocket. Instead of high pressure "blow down" system, an Electric Feed System (EFS) will be used to provide the necessary pressure to pump the propellants into the engine. The EFS has been prototyped and de-risked in a previous capstone, but was not revised and is not able to be used in flight. This capstone will take the previous capstone's work and optimize it for flight in LV4, PSAS' future liquid oxygen and isopropyl alcohol rocket.

## Customer needs

The goal of this project is to create a cryogenic-capable bi-propellant electric feed system with the following criteria:

- Must be compatible with liquid oxygen (LOX) and isopropyl alcohol
- Must safely keep the propellants separated until injection into the engine even in the event of a pump failure
- Must be able to be used on the PSAS engine test stand
- Must be able to operate without overhaul for multiple rocket engine test fires (≥ 10 firings)
- Must handle launch environment, including vibration and an acceleration of 10 g for 20 seconds.
- Should have embedded sensors for data acquisition, feedback, and control
- Should be plumbed efficiently to minimize pressure loss
- Must deliver propellants at 300-500 PSI from a tank at 45-70 PSI.

## Typical operation or user interaction

The EFS will be used on the test stand, and eventually in a future PSAS rockets. During each test and flight, the pump will be responsible for safely and consistently delivering pressurized liquid oxygen and isopropyl alcohol to the rocket engine at the correct pressure and mass flow rate.

## Financial and in-kind support

PSAS will supply building materials and electrical support for this project. Up to $2,000 for funds are allocated, but cost effective design is highly desired to minimize the overall cost.

## Special requirements

- All intellectual property must be assigned to PSAS, and the project will be open source under the CERN OHL v1.2 license.
- Team members must use SolidWorks for CAD work design.
- Chemical safety training will be required for all members handling LOX
- All project design and documentation must be done using git on PSAS' Github pages.
- Shop access will be required for students who will be machining components
- Team members are expected to attend most Tuesday evening PSAS meetings from 7:00pm - 8:00pm. However, at least ONE team member must give an update at PSAS' standard Tuesday evening meeting, either in person in FAB 86-01 or via Google Hangouts.
- All team members must agree to and sign the PSAS New Member Agreement.
- All team members must register for the Base 11 Space Challenge.

## Deliverables

- Full and complete documentation including:
  - Background, including research done and theory of operation
  - CAD models for entire pump system
  - Safety analysis and SOPs, including full FMEA of the pump system
  - SOPs for mounting, operation, and requirements
- A functioning prototype that’s been tested for
  - Chemical compatibility
  - Operating temperature conditions
  - Performance and efficiency
  - Vibrational disturbances
  - Control signal data
  - Estimation of reliability

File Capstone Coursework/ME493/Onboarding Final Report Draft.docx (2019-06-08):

Create Awesome title page with the following content

- Report Title
- Team Members
- Date of the Report
- Name of Sponsoring Company
- Academic/Industry Advisors
- Include the sentence
  - “ME 493 Final Report: Spring 2019”

Outline

1. Executive Summary
2. Table of Contents
3. Introduction and Background Material
4. Mission Statement
5. Main Design Requirements
6. Brief Discussion of the top-level alternative conceptual solutions, the chosen design, and justifications to strengths of the chosen design
7. The final design (easy to understand format)
8. Present the results of various evaluations as required by PDS
9. Conclusions and Recommendations
10. All supporting materials [Appendices]

Begin working creating and edit sections below this page.

Executive Summary

Portland State Aerospace Society (PSAS) requires a Flight-Ready Electric Feed System for their upcoming Launch Vehicle 4 (LV4). An Electric Feed System (EFS) is an electronically controlled pump system used to provide the necessary pressure to deliver liquid propellant to the engine. The EFS must be cryogenic compatible to withstand the environment that the liquid oxygen (LOX) and isopropyl alcohol (IPA) propellants create. While this project has yet to provide a flight-ready system, significant headway was made on developing a cryogenic compatible system. Improvements were made upon the previous design, and recommendations on how to proceed are being drafted for future EFS design teams.

Blue means pull from winter document, green means done

Table of Contents

1. Introduction
2. Mission Statement
3. PDS
4. Concept Designs
  4.1. Single Engine - Twin Pumps
    4.1.1. Axial Inline Pump
    4.1.2. Axial Split Single Suction
    4.1.3. Barrel Pump with Bevel Gears
  4.2. Twin Engine - Twin Pumps
5. Final Design Selection
  5.1. Material Properties
  5.2. Impeller Design
  5.3. Machinability
  5.4. Power Components
  5.5. Internal Components (seals-bearings)
  5.6. Test Assembly
6. Pump Result Breakdown
  6.1. IPA Pump Performance
    6.1.1. Test One
    6.1.2. Test Two
    6.1.3. Test Three
  6.2. Cryo Pump Performance
    6.2.1. Test One
7. EFS Onboarding
  7.1. Pump System Mechanics
  7.2. Design Goals
  7.3. Recommendations
  7.4. Continuing Design
    7.4.1. LV4 Integration
      7.4.1.1. Test Stand
      7.4.1.2. LV4 Airframe
    7.4.2. Pump Internals
      7.4.2.1. Bearings
      7.4.2.2. Seals
      7.4.2.3. Alignment
    7.4.3. Testing Procedures
8. Conclusion
9. Appendices

1. Introduction

The final system deliverable is expected to meet the following chemical compatibility, operating temperature conditions, performance efficiency, vibrational disturbances, and control signal data. PSAS also expects complete documentation of background research procedures for pump mounting and operations. Final deliverables must be within budget and completed by June 2019.

2. Mission Statement

The Electric Feed System Capstone aims to provide affordable, lightweight propulsion system technology to increase the capabilities of amateur rocketry and student education.

3. Product Design Specifications (PDS)

PSAS provided baseline requirements for the project to outline the expectations and reach goals for this Capstone. Tables 1 outlines and ranks the customer needs from highest to lowest priority items, with 5 being top priority, as of May 2019. The Customer needs to outline the necessary design requirements metrics are shown in table 2, and the derived engineering requirements are shown in table 3.

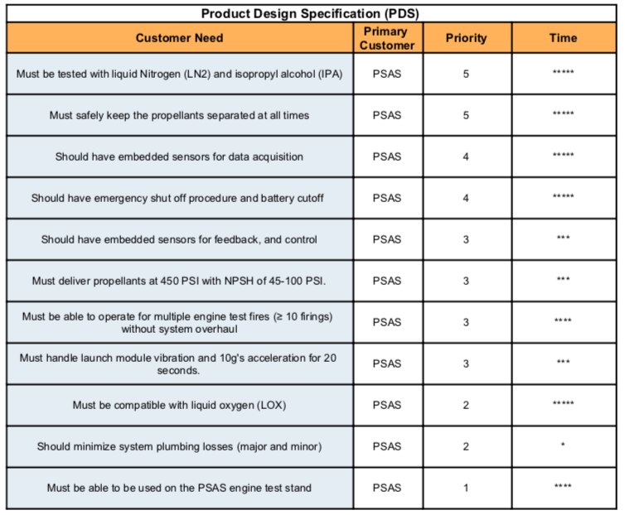
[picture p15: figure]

Table 1: PSAS customer needs for the Electric Feed System Capstone Team ranked by priority

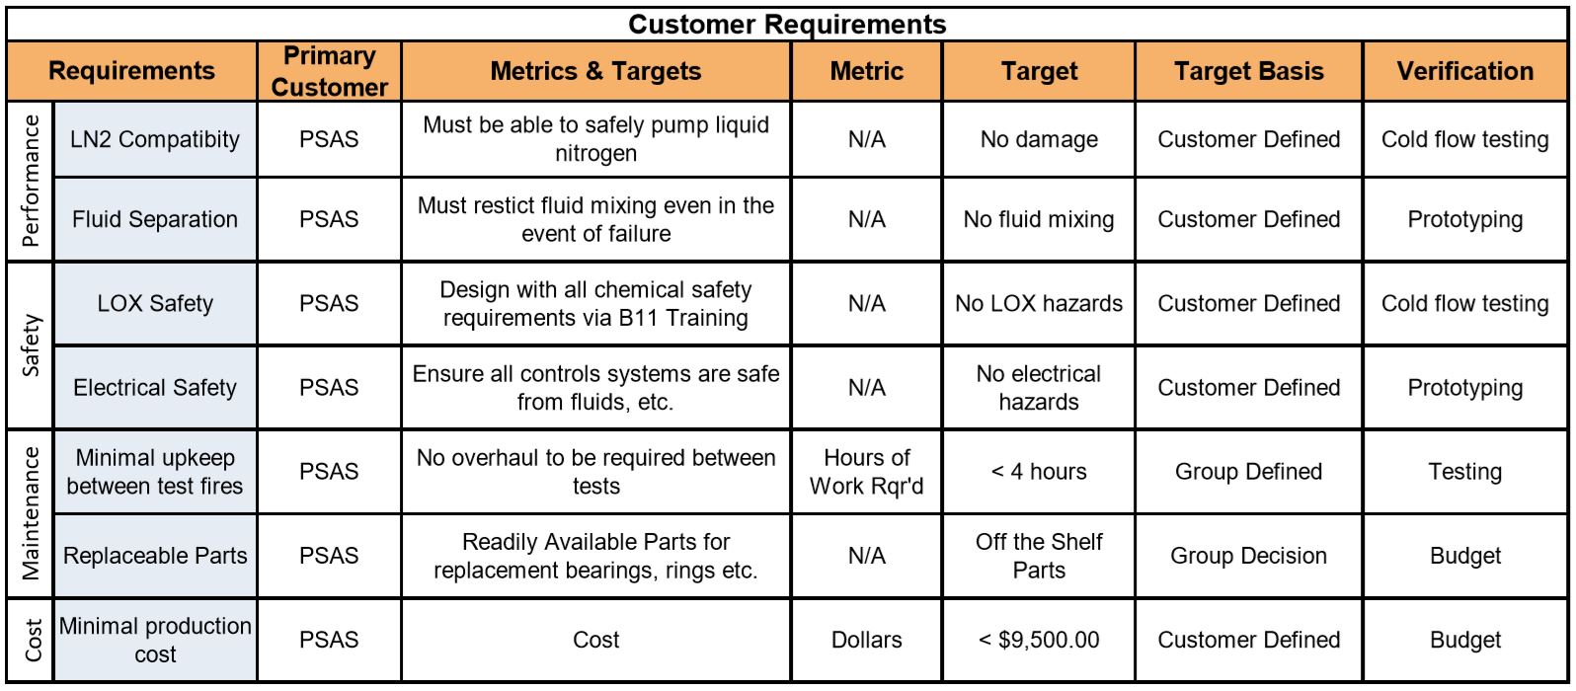
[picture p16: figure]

Table 2: EFS Customer Design Metrics

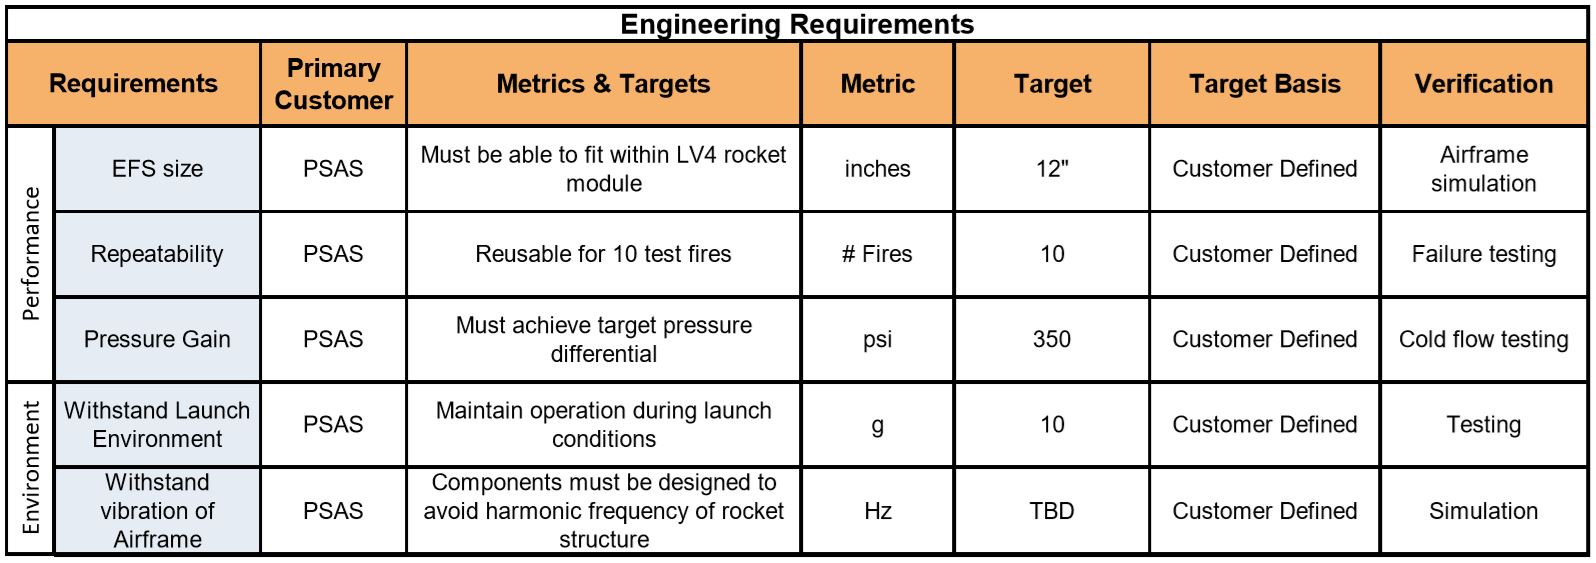
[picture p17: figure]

Table 3: EFS Engineering Design Metrics

4. Concept Design

The following sections provide the background to previous design ideas for the electric feed system pumps leading to the final manufactured design.

4.1 Single Drive Dual Pump Design

Initially, the EFS was conceptualized as a pumping system in which two centrifugal pumps were driven by a single power source. The goal of this design was to decrease the total space and weight used by the electric feed system by reducing the need for a second motor.

4.1.1 Axially Split Inline Pump

The first design concept for the EFS featured two pumps with axially split pump cases running inline with the same drive shaft. The center pump would have a pass-through shaft with bearing housings on either side of the pump to allow the shaft to continue out to drive the second pump, as shown in Figure ##.

While the use of a single drive in this context would reduce the weight of the system by the removal of one motor, it was concluded that this design was not feasible after preliminary hydraulic calculations were made. Each fluid requires a different rotational speed to achieve the appropriate pump specific speed required for suction[1], so it was concluded that the two pumps could not share a drive directly.

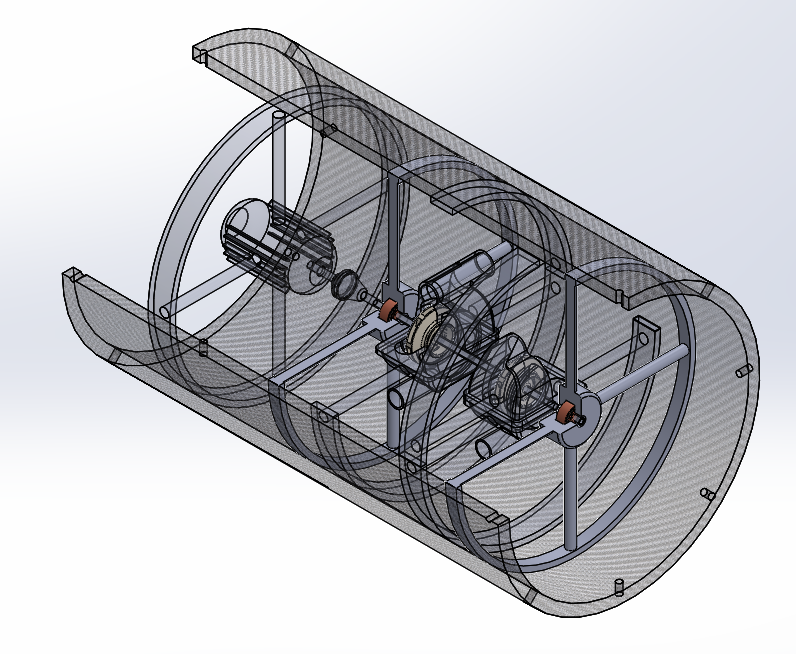
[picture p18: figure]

4.1.2 Barrel Pump with Bevel Gearbox Drive

Given the issues with running a single drive inline, a design was generated that featured a single motor used to drive a bevel gearbox. Both pumps were then run orthogonally from the direction of the motor shaft, as shown in Figure ##.

This design would allow for separate rotational speeds by utilizing gear ratio relationships to drive the two pumps at different rates. However, this would require a motor with very high power density, which was determined to be outside of the scope of the project budget. Additionally, the use of a gearbox would result in larger amounts of energy loss and overall system inefficiency, which would not be optimal for integration into the rocket. Moreover, the energy lost to the gearbox would result in a large amount of heat generation in close proximity to the flow region of the cryogenic fluid, resulting in two-phase flow and risk of cavitation in the LOX pump.

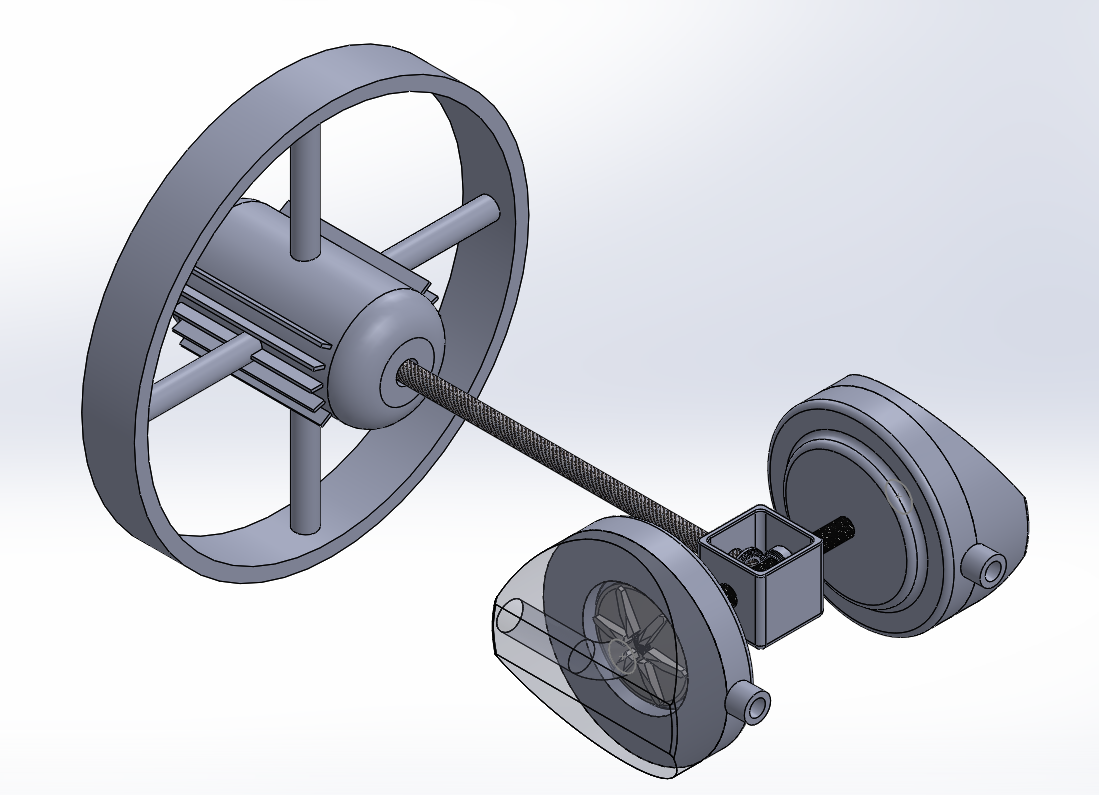
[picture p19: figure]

4.2 Dual Drive Parallel Pump Design

The optimal pump orientation was decided to be two pumps running parallel to each other on separate drive shafts. While the second motor and mount add additional weight, the system is more reliable and more effective overall, as two motors with the required separate power densities can be procured for less than the cost of a larger single shaft drive system with comparable power density. Additionally, this design allowed for the fabrication and testing of initial prototypes for IPA while design and analysis continued to be performed for the LOX system.

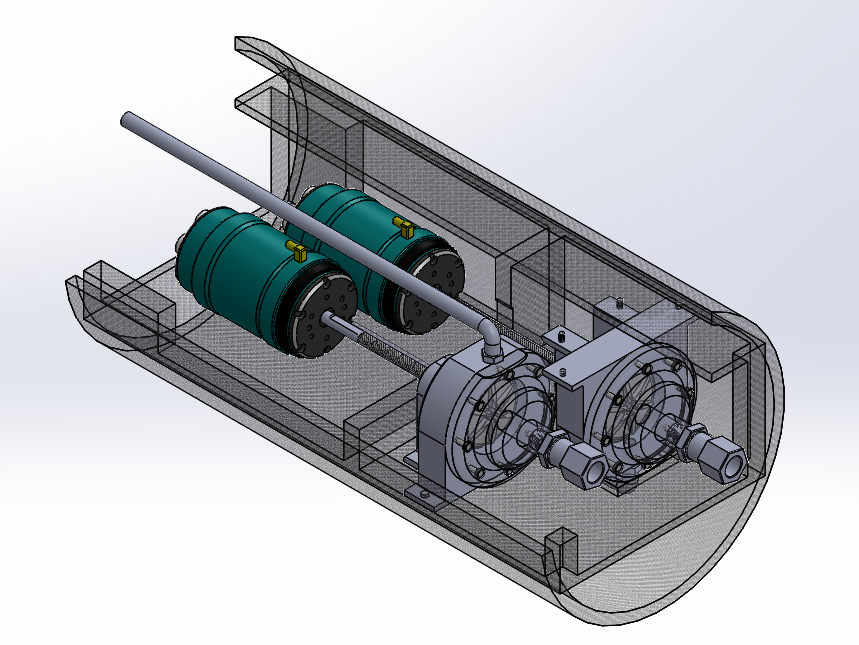
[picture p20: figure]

5. Final Design Selection

The dual drive option was selected as the optimal power system configuration, as it allows for the greatest level of independence for rotation speeds between the two fluid pumps while remaining reliable and cost-effective. The final design consists of a three-piece pump housing that is assembled piecewise along the shaft axis, as shown in Figure ##. The two assembled housings are mounted into the corners of the module mount, fastened in an orthogonal pattern to handle shock and vibration symmetrically in the XY plane. The final design’s motor is mounted to the pump housing itself rather than the module mount, as this ensures optimal alignment from the drive shaft to the impeller, as shown in Figure ##. flow is plumbed downward into the impeller eye opposite to the rocket’s acceleration direction in order to achieve the flow rate calculated based on the rocket’s ideal thrust. The outlet plumbing exits the side of the pump and is fed down to the engine.

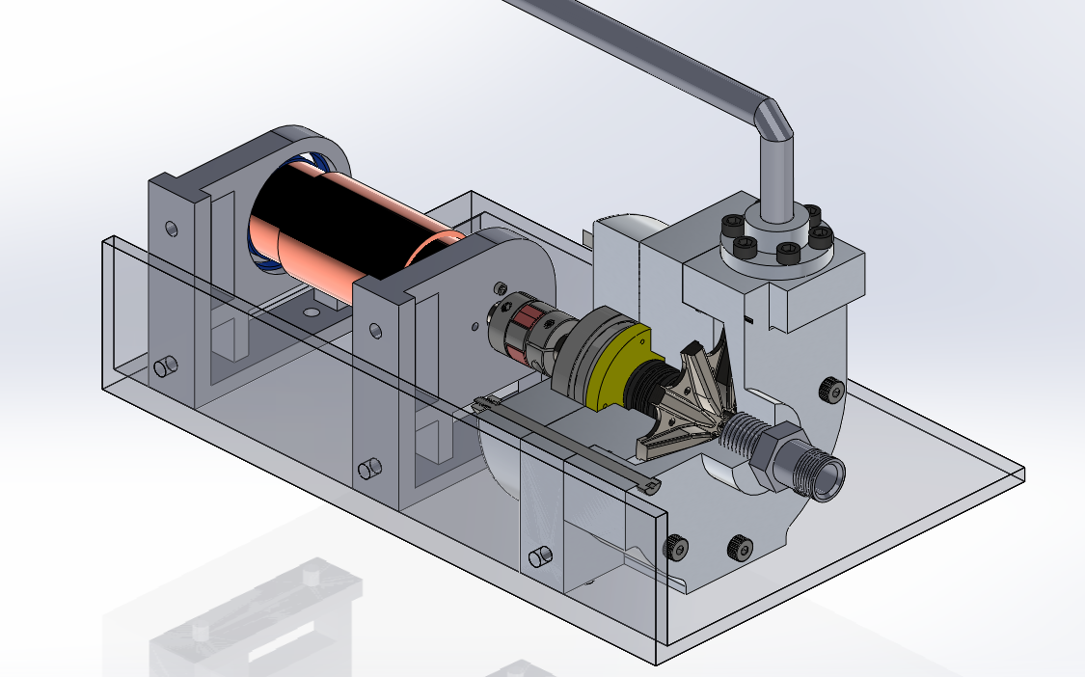
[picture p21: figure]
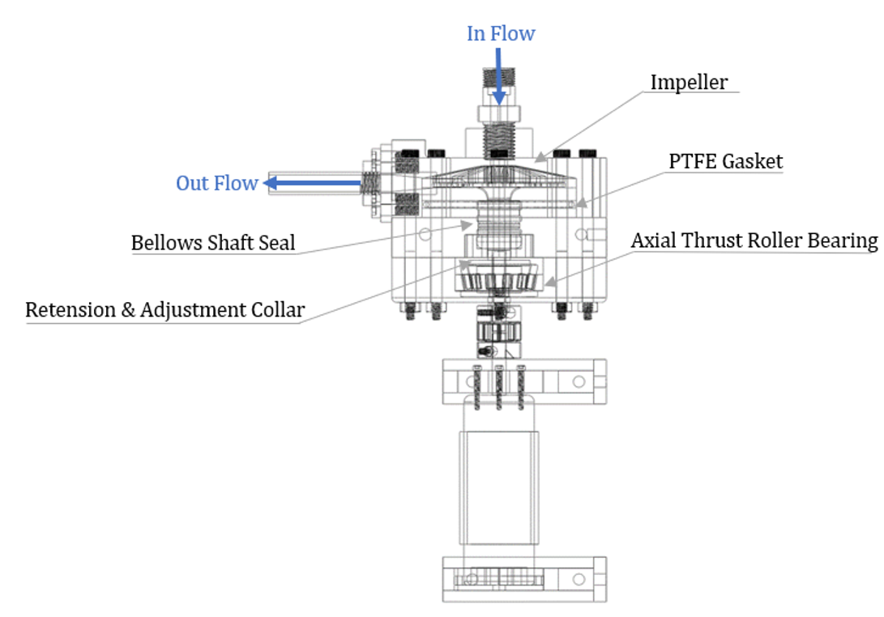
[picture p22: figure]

5.1 Material Properties

Research in material properties and compatibility led to the selection of Aluminum 6061 for the fabrication of both the isopropyl alcohol and liquid oxygen pumping systems. The primary factor impacting this decision was material compatibility with LOX. Because of the volatile properties of liquid oxygen, material selection for this fluid required the consideration of a number of safety and reliability factors, including oxidation, corrosion, and cavitation. It was decided that an aluminum alloy would be the safest selection based on the research performed in these areas.

6061 was selected as the ideal alloy for this project’s application, as it is relatively low-cost and is more machinable than stainless steels, which were also considered for use. This allowed for more practical in-house fabrication, lowering the cost of production and lead times.

The material behavior of this alloy was also determined to be the most desirable for cryogenic applications. While most stainless steels may have higher strengths and lower tendencies to oxidize, it was found that aluminum 6061 is more ductile at cryogenic temperatures than any of the stainless steels researched. At the pressure magnitudes required for the electric feed system to operate, loss of ductility generated risk of ductile-to-brittle transition for the stainless steels considered.

Table ##: Material Selection Matrix

Material | Mechanical Properties | Machinability | Cost | Extreme Temperature Performance | LOX Compatibility | Score
Aluminum 6061 | 3 | 5 | 5 | 3 | 2 | 18
Aluminum 7075 | 3 | 5 | 2 | 3 | 3 | 16
SS 304 | 5 | 1 | 2 | 1 | 5 | 14
SS 316 | 5 | 1 | 2 | 1 | 5 | 14

5.2 Impeller Design

In EFS pumps, a specialized impeller is required to provide high-pressure gains while maintaining a low flow rate. Taking into consideration the previous team’s research as well as industry literature on liquid propellant rockets, we found a Barkse impeller design to be the most favorable for this application. These impellers are intentionally designed to be inefficient. This inefficiency allows for large pressure gains while maintaining low flow rates. The previous team also tested a variety of impeller designs with a varying number of vanes. It was found that 10 vanes were the most efficient number of vanes for the pump.

Another critical design decision involved in the impeller was the impeller and shaft connection interface. The impeller needed to be able to withstand high torque values and be machinable within the campus machine shop. The final design evaluation for the impeller resulted in the selection of a single-piece shaft. It was determined that this design could be made in-house at PSU from 3” diameter, 3 ¾ long raw stock 6061-T6 aluminum. This design scored the highest against the matrix design criteria and was selected to move forward with to begin prototyping.

5.3 Manufacturing

- Machines available
- Tooling available
- Flexibility with functional prototypes
- Decision to manufacture in house. Reduced costs

5.4 Power Components

The requirements for shaft power led us to select a TP Power 4070CM as the BLDC motor for the IPA pump along with a Swordfish 200A electronic speed controller (ESC). Including the batteries and other accessories, this combination was within budget, at around $1000, and well exceeded the requirements for the IPA system. Purchasing an overpowered motor for the IPA pump increased our design efficiency by replicating the components to the cryogenic pump after testing and fine tuning is completed. The use of identical motor systems for both pumps saved time and freed up to focus for other components.

Safe operation is a strong requirement for the system to be considered successful. This project is to focus on designing for the flight which entails autonomous operation for the EFS. When selecting the ESC, batteries, and connectors, safe autonomous operation during the flight was prioritized by PSAS for the team. Gold plated, 8mm bullet connectors are found along with the entire wire harness because they offer a safety factor of 1.75 against high current load damage. This minimizes the risk of meltdown and electrical fires. The batteries powering the motor have a 350A capable discharge rate which provides a 1.88 safety factor, once again, against fires due to meltdown or damage from high current demand from the motor. Lastly, the Swordfish 200A ESC provides a built-in water cooled case for heat dissipation and a safety factor of 1.34 against damage due to high current.

5.5 Internal Components

Phil

5.6 Test Assembly

To facilitate quick testing, a mobile test stand was used to

6. Pump Results Breakdown

6.1 IPA Pump

6.1.1 Test One

Test one of the full IPA pump assembly was performed after all machined components were completed. Initial setup of the system proved difficult as we discovered there was not an accurate method for positioning the components along the shaft. Our design called for clearances as small as 0.008 inches between parts and there was no way of measuring the internal component positioning. The greatest risk associated with the unknown positioning was the impeller contacting the inside of the pump housing. To monitor this possibility, the inside of the pump housing was painted so disturbances could be observed after testing was completed.

To begin testing, we slowly turned the potentiometer on so that the motor would start at a lower speed. Immediately upon startup, rubbing and churning noises came from the system. With no obvious sign of what was making the noise, we cut the test immediately. After inspection of all external components and still no sign of interference, we tried them again. The same noises ensued, however, this time we decided to keep the system running a few moments longer to see if things would pick up and engage. During the second attempt, a loud pop came from the ESC and the system came to a halt. The ESC had. We suspected this was either from an overload in current or water entering the ESC housing.

The system was disassembled and inspected for the further prognosis of the unknown noise. Scratches were found in the paint on the inside of the pump housing which verified contact of the impeller. We did not believe this was the cause of the noise. Discussion among group members revealed the difficulty that existed in turning the impeller by hand. Questions arose around whether there were inaccuracies within the concentricity and alignment of the components. The noises were thought to have come from two or more internal components rubbing on each other. Other possibilities left open for investigation were the possibility of bearing wobble, sticking seals, and too much tension in the seals.

Further time would need to be invested into the cause of the short-circuited ESC and failed test. A replacement ESC was ordered and all internal components were evaluated after testing.

6.1.2 Test Two

After the first test, we were able to diagnose some of the issues and made some modifications to the pump case. In order to release the tension that been put on the seal, the lower pump case was been re-machined. This time we increased the inside diameter of the lower casing. By doing that, we let the dynamic seal made contact directly with the lower face of the impeller. The result showed us that the tension on the seal was released. The reason we did that is to decrease the pressure that been put on the impeller and to make it spin freely with no contact with either of the faces. After the new ESC had arrived, we came up with the countermeasure for it. We used the hot glue and sealed the open areas in order to isolate the circuit board from the outside atmosphere to prevent the water been leaked in.

The second test was implemented after all of the problems have been fixed. The test procedure was strictly followed by the first test. After the power been turned on, there was no problem in the control circuit, as we turn up the speed of the motor, the noise started to get loud, after a few seconds, there was a electric spark appeared around the ESC. We immediately aborted the test, because we were afraid that the new ESC would be destroyed. The similar problem has appeared at the second test. We disassembled the entire system and tried to find the problem.

After the pump takes down from the test stand, we were found that the motor was still hard to turn with the impeller shaft. After the pump casing was separated, we found that there was a scratch on the inside of the upper casing, the cause of that was due to the impeller been contacted with the face of the case. When we separated the bearing case with the lower case, there was water leaked into the gap between those two faces. We were assuming that making the seal in contact with the impeller has made the seal lost efficacy. As the seal not only lost the function as a dynamic seal but obstructed impeller moving freely. Because there was such a big force was put on the motor, it was also increased the resistance on the circuit board which caused the power surge that fried the component of the circuit.

We were trying to see if the ESC was able to work again without everything being put on the motor. The result showed that the component that communicates with the motor was damaged, so the ESC was not working properly, and a replacement has to be ordered. As we examed every component been put on without the upper case, we also found that there was an alignment issue. As we tied up the coupler, the impeller shaft and motor shaft were not aligned, which would also cause the one side of the impeller been touched with the upper case. Based on all of the problems, the proper measures were been used to the new cryogenic pump design.

6.1.3 Test Three

6.2 Cryo Pump

7. EFS Onboarding

7.1 Design Goals

7.2 Recommendations

7.3 Continuing Design

7.3.1 LV4 Integration

7.3.1.1 Test Stand

7.3.1.2 LV4 Airframe

7.3.2 Pump Internals

7.3.2.1 Bearings

7.3.2.2 Seals

7.3.2.3 Alignment

7.3.3 Testing Procedures

8. Conclusion

9. Appendix

* Insert Finished Gantt Chart

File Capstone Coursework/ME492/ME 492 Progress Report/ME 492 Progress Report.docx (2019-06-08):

TITLE PAGE

EXECUTIVE SUMMARY

Portland State Aerospace Society (PSAS) aims to design, build, and test an Electric Feed System (EFS) prototype using commercial off-the-shelf parts and in-house manufacturing. Currently, CAD designs have been finalized and selection for several key components have been chosen including the impeller design and shaft connection, motor, and design for the pump housing. This report details the requirements and selection process criteria for these components. Progress on detailed design is also discussed.

TABLE OF CONTENTS

1. INTRODUCTION

Portland State Aerospace Society (PSAS) requires a Flight-Ready Electric Feed System for their upcoming Launch Vehicle 4 (LV4). An Electric Feed System (EFS) is an electronically controlled pump system used to provide the necessary pressure to deliver liquid propellant to the engine. The EFS must be cryogenic compatible to withstand the environment that the liquid oxygen (LOX) and isopropyl alcohol (IPA) propellants create. In traditional amateur rocketry, a high pressure "blow down" system is used to deliver propellant to the engine. These systems are costly and require heavy fuel tanks causing them to be less than ideal for launch. Creating an EFS as an alternative to a pressurized tank is a challenging and innovative task that this capstone hopes to achieve.

2. MISSION STATEMENT

The Electric Feed System Capstone aims to provide an affordable, lightweight propulsion system technology increasing the capabilities of amateur rocketry and student education.

The final deliverable to be presented to PSAS is expected to be tested for the following: chemical compatibility, operating temperature conditions, performance and efficiency, vibrational disturbances, control signal data, and estimation of reliability. PSAS also expects complete documentation of the following: background (research done and theory of operation), CAD models for entire pump system, safety analysis and standard operating procedures for mounting and operation (including full FMEA of the pump system). Final deliverables must be within budget and completed by June 2019.

3. PROJECT DESIGN SPECIFICATIONS (PDS)

Portland State Aerospace Society has defined the requirements for the EFS capstone. Table B: Product Design Specifications summarizes the customer needs and their ranking of priority upon final completion. Table C: Customer Requirements and Table D: Engineering Requirements cover targets and metrics along with our verification process for achieving these.

Table B. Product Design Specification

Product Design Specification (PDS)
Customer Need | | | Primary Customer | Priority | Time
Must be tested with liquid Nitrogen (LN2) and isopropyl alcohol (IPA) | | | PSAS | 5 | *****
Must safely keep the propellants separated at all times | | | PSAS | 5 | *****
Should have embedded sensors for data acquisition | | | PSAS | 5 | *****
Should have emergency shut off procedure and battery cutoff | | | PSAS | 5 | *****
Should have embedded sensors for feedback, and control | | | PSAS | 4 | ***
Must deliver propellants at 450 PSI with NPSH of 45-100 PSI. | | | PSAS | 4 | ***
Must be able to operate for multiple engine test fires (≥ 10 firings) without system overhaul | | | PSAS | 3 | ****
Must handle launch module vibration and 10g's acceleration for 20 seconds. | | | PSAS | 3 | ***
Must be compatible with liquid oxygen (LOX) | | | PSAS | 3 | *****
Should minimize system plumbing losses (major and minor) | | | PSAS | 2 | *
Must be able to be used on the PSAS engine test stand | | | PSAS | 1 | ****

Table C. Customer Requirement

Customer Requirements
Requirements | | Primary Customer | Metrics & Targets | Metric | Target | Target Basis | Verification
Performance | LN2 Compatibity | PSAS | Must be able to safely pump liquid nitrogen | N/A | No damage | Customer Defined | Cold flow testing
| Fluid Separation | PSAS | Must restict fluid mixing even in the event of failure | N/A | No fluid mixing | Customer Defined | Prototyping
Installation | Manpower to test | PSAS | Manpower | # People | 4 People | Customer Defined | Cold flow testing
| Time to replace spare parts | PSAS | Time | Mins | 2 Hours | Team Defined | Timed after prototype built
Safety | LOX Safety | PSAS | Design with all chemical safety requirements via B11 Training | N/A | No LOX hazards | Customer Defined | Cold flow testing
| Electrical Safety | PSAS | Ensure all controls systems are safe from fluids, etc. | N/A | No electrical hazards | Customer Defined | Prototyping
Maintenance | Minimal upkeep between test fires | PSAS | No overhaul to be required between tests | Hours of Work Rqr'd | < 4 hours | Group Defined | Testing
| Replaceable Parts | PSAS | Readily Available Parts for replacement bearings, rings etc. | N/A | Off the Shelf Parts | Group Decision | Budget
Cost | Minimal production cost | PSAS | Cost | Dollars | < $9,500.00 | Customer Defined | Budget

Table D. Engineering Requirements

Engineering Requirements
Requirements | | Primary Customer | Metrics & Targets | Metric | Target | Target Basis | Verification
Performance | EFS size | PSAS | Must be able to fit within LV4 rocket module | inches | 11.3" | Customer Defined | Airframe simulation
| Repeatability | PSAS | Reusable for 10 test fires | # Fires | 10 | Customer Defined | Failure testing
| Pressure Gain | PSAS | Must achieve target pressure differential | psi | 350 | Customer Defined | Cold flow testing
Environment | Withstand Launch Environment | PSAS | Maintain operation during launch conditions | G-force | 10 | Customer Defined | Testing
| Withstand vibration of Airframe | PSAS | Components must be designed to avoid harmonic frequency of rocket structure | Hz | TBD | Customer Defined | Simulation

4. PROJECT PLANNING

To promote progress in all divisions of the EFS design, our team was divided into two groups. The first group’s efforts were focused on finalizing design and the controls for the motor. The second group began prototyping the IPA pump housing, impeller, and motor mounts. To assure members of the team had clearly defined tasks and were able to meet deadlines, a Gantt chart was created. Table A. illustrates the timeline of completion while highlighting priority and the individuals assigned to each task.

Table A. Electric Feed System Project Schedule

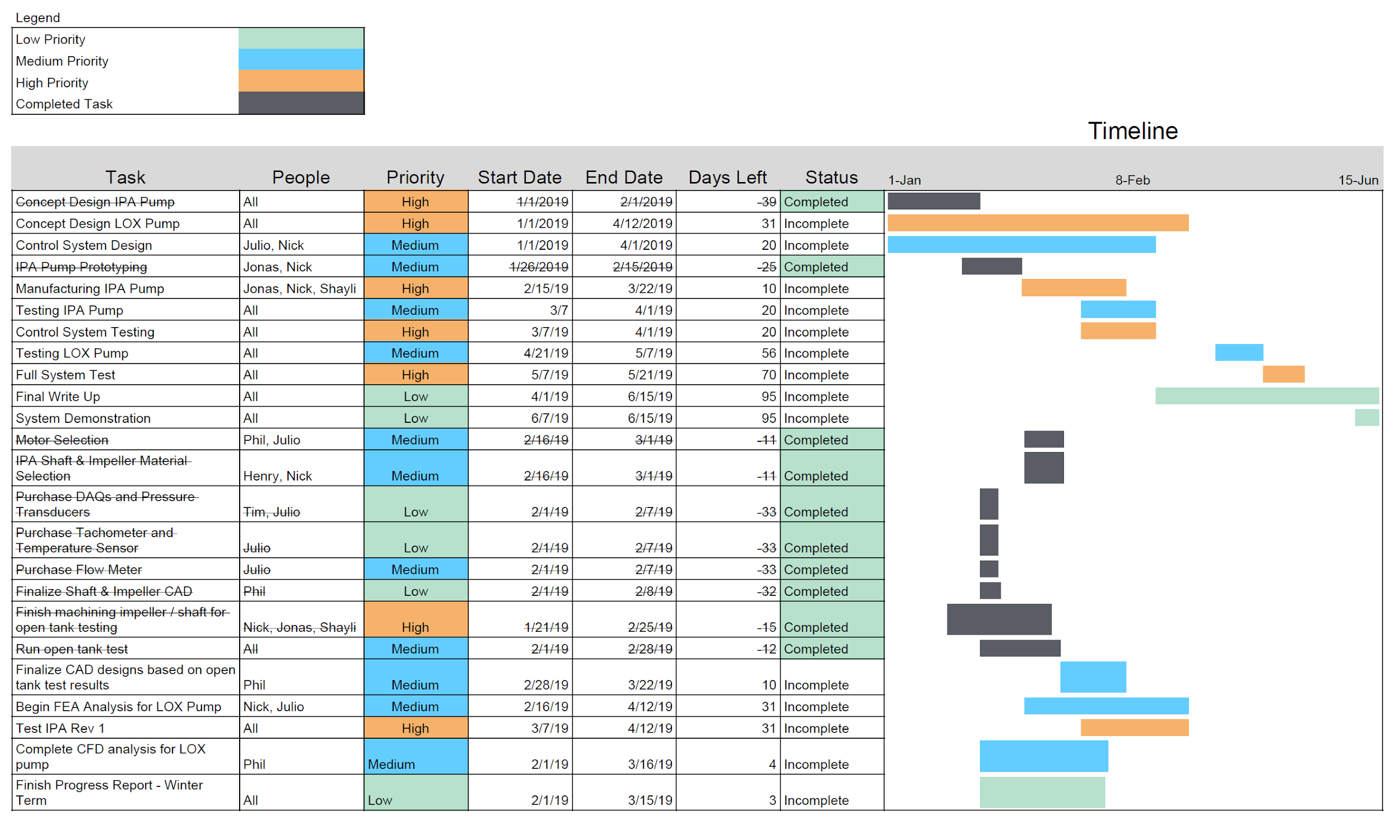
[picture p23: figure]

5. EXTERNAL SEARCH

The team’s main focus for this term was to design and test the IPA pump. In order to move forward, the IPA pump’s impeller and housing needed to be designed and a motor needed to be selected.

5.1 IMPELLER

In EFS pumps, a specialized impeller is required to provide high pressure gains while maintaining a low flow rate. Since this project is a part of an iterative design spanning multiple capstones, we started by looking at the previous capstone team’s work. Their research found that a Barske impeller design is the most ideal design for this application. Our team reviewed industry literature on liquid propellant rockets to verify that Barske impellers are commonly used for this application. These impellers are intentionally designed to be very inefficient. This inefficiency allows for large pressure gains, while maintaining low flow rates. The previous team also tested a variety of impeller designs with varying number of vanes. It was found that 10 vanes was the most efficient number of vanes for the pump.

5.2 MOTOR SELECTION

With a 30,000 RPM impeller rotation during operation, it was important that the selected motor be capable of continuously providing the necessary rotational speed without strenuous efforts. The motor also needed to quickly and accurately respond to flow characteristics via a feedback control system with integrated sensors. A previous EFS capstone design steered us towards the use of a high output RC boat brushless DC (BLDC) motors due to the relative success they achieved with this affordable motor option. Comparing system requirements showed the need for more power and controllability than previously achieved. Through fluid flow and geometric calculations, 2 kW of power, 0.6 N*m of torque, and approximately 30,000 RPM were identified as the factors for motor selection.

5.3 PUMP HOUSING

The most apparent feature of the previous year’s capstone that we wanted to address in our design was the pump housing. We recognized that keeping the pump housing in sections made for easy assembly and manufacturability. Our challenge was in how to reduce the weight and overall bulk of the first iteration. Although not specifically requested by PSAS, a large target for our design this year was weight reduction. We began to evaluate shape and material to determine if any sections could be altered.

6. INTERNAL SEARCH

During weekly meetings in the design phase, sketches and CAD models were displayed for the group to evaluate. This dedicated time gave teammates an opportunity to express concerns in design or alternatively, allowed the group to collectively agree upon the final design for any given component.

6.1 IMPELLER

The previous team’s impeller was manufactured using direct laser metal sintering (DLMS), an additive manufacturing process that is essentially 3D printing with metal. While this process allows for complex geometry that is often difficult or impossible to create with conventional machining processes, it cannot achieve as high of dimensional precision as machining can. Additionally, due to the nature of metal sintering, parts produced via this method are more porous than parts machined from solid billet. This became an area of concern for the team for two reasons.

First, in order for the impeller to function properly, it must have a very small clearance between the pump housing and itself. The smallest of these clearances in our design is 0.008” inches. The dimensional resolution possible with DLMS was deemed too unreliable, as the tolerance on these parts may allow the impeller to contact the wall of the impeller chamber. Further, geometric inconsistency would likely cause the impeller to become unbalanced when rotating at the 30,000 + rpm required for our design. Second, the porosity present in sintered parts was of concern considering the impeller would be rotating at high speed. While the system is only expected to transmit approximately 1.1 N-m of torque through the impeller under steady-state conditions, porosity could allow cracks to form and propagate throughout the impeller geometry under operating conditions. This would likely cause catastrophic failure in the entire rocket system should the pump fail, or fragments of material enter the fuel line. Taking these conditions into consideration, the team decided to move forward with machining the impeller in-house, using the CNC machines available on campus.

Once the impeller material and manufacturing processes had been reviewed, the team began to analyze potential designs for mating the pump shaft with the impeller. The previous team incorporated a small hub on the backside of the impeller that had a hole bored out for the pump shaft. A pin was inserted into matching cross-holes on the hub and shaft in order to connect the two components. Our team had some concern with this design and whether or not it may actually weaken the shaft, given the cross-hole diameter was relatively large compared to the shaft diameter. The reduction in shaft cross-section could introduce stress concentration problems if the inserted pin didn’t create a tight fit. The team began to analyze alternative methods to connect the shaft to the impeller.

The first alternative to using a pin was to create a sort of lobed shape on the end of the shaft, that would fit into a mating hole in the hub of the same shape. This design would allow the shaft to spin the impeller without slipping, since the shaft would only connect to the hub in one orientation. However, the team realized that this design would not prevent the impeller from sliding forward on the shaft in the axial direction, and potentially hitting the front of the impeller chamber. In order to prevent this motion, a set screw or pin would need to be incorporated, further weakening the design. Additionally, a lobed shape would introduce further complexities in the manufacturing process. A lobed shape was prefered for this design since it would remove sharp edges, and thus stress concentrations, in both the shaft and hub.

The next shaft-impeller design explored using a “keyed” shaft, where a shallow rectangular slot would be cut on the outside diameter of the shaft, along the axial direction. A matching slot would be cut inside the hub’s bore, and then a rectangular “key” would be used to fill the space between the shaft and hub, allowing the shaft to spin the impeller. We realized that this design would also require the use of a set screw to prevent the hub and shaft from separating. However, in this case a set screw could simply pass through the hub and press down on the key. Doing so would not require any additional features to be cut onto the shaft, thus maintaining the integrity of the shaft.

The challenge with the keyed design became apparent when the required machining process was taken into consideration. While a slot could easily be cut on the shaft, we would need to broach the hub in order to cut the mating slot. Broaching, a material in which small amounts of material are sheared away, requires very specific tooling to be performed inside a blind hole. Since this tooling isn’t readily available on campus, the team would need to purchase the supplies. The required tooling to broach just the hub slot would have cost around $450.00. Further, a broaching operation requires a groove to be cut deeper inside the hub bore to provide “relief” for chips formed during the broaching operation, or else the tool will bind up and break. This relief groove would require the purchase of additional tooling, and significantly weaken the hub. The team decided that prototyping this design would be too expensive, and would potentially result in a weaker assembly than the previous two potential designs (pin and lobe).

Taking into consideration the possibility of inefficient torque transmission from the motor to impeller due to various connections between different components, the team continued to look for alternative designs. The team began to explore the idea of using a solid state impeller-shaft design, in which the impeller and shaft would be one single component. Combining the shaft and impeller removes the need for a hub. Without the hub, this design would allow material reduction on the impeller itself, but would also allow the pump housing the be thinner, and thus further weight reduction. Concerns with design arose considering the change in diameter from the shaft to the outer diameter of the impeller. The largest diameter of the impeller is around 8 times larger than the shaft diameter. It was a concern that stress concentrations at the shaft-impeller interface could lead to failure. The team reviewed the torque requirements and the material properties of AL 6061-T6, and decided that the low torque would not be enough to cause failure. However, to guard against failure, a large fillet was place at the shaft-impeller interface, thus easing the transition in diameters.

The team decided that the solid state shaft-impeller design was the most promising option, and set out to verify this assumption with design scoring metrics before moving forward with prototyping.

6.2 MOTOR SELECTION

The requirements for shaft power led us to selecting a TP Power 4070CM as the BLDC motor for the IPA pump along with a Swordfish 200A electronic speed controller (ESC). Including the batteries and other accessories, this combination was within budget, at around $1000, and well exceeded the requirements for the IPA system. Purchasing an overpowered motor for the IPA pump increased our design efficiency by replicating the components to the cryogenic pump after testing and fine turning is completed. The use of identical motor systems for both pumps saved time and freed up focus for other components.

Safe operation is a strong requirement for the system to be considered successful. This project is to focus on designing for flight which entails autonomous operation for the EFS. When selecting the ESC, batteries, and connectors, safe autonomous operation during flight was prioritized by PSAS for the team. Gold plated, 8mm bullet connectors are found along the entire wire harness because they offer a safety factor of 1.75 against high current load damage. This minimizes the risk of meltdown and electrical fires. The batteries powering the motor have a 350A capable discharge rate which provides a 1.88 safety factor, once again, against fires due to meltdown or damage from high current demand from the motor. Lastly the Swordfish 200A ESC provides a built in water cooled case for heat dissipation and a safety factor of 1.34 against damage due to high current.

6.3 PUMP HOUSING

It was determined that the front case of the housing needed to be machined on three of its sides. Being limited by a three axis vertical mill, the profile of the front case was modified to have flat surface that allowed a secured set up for the side operation. CAD/CAM simulation models helped determine the dimensions of the flat without sacrificing wall thickness. Pipe thread analysis from the machinery’s handbook and past experience from team members contributed to the selection of main hardware for the housing and plumbing connections.

Alignment between front and back housing cases when assembled was a concern, and two solutions to approach this issue were evaluated. First solution was to use small dowel pins press fitted on the front case, allowing the back case to align itself to the front case when assembled. This solution was supported by previous successful results from past projects under similar conditions. The second solution was to machine oversize holes on the front case and to use precision shoulder bolts that would allow the back case to slide in place using the ground shoulder as a guide. Based on the hardware specifications provided by manufacturer, the team concluded that the precision shoulder bolts would be the best solution due to the tolerance and surface finish of the ground shoulder bolts, and the time saved by eliminating an extra machining operation.

7. FINAL DESIGN EVALUATION

Criteria influencing decisions made to move from design to prototyping were thoroughly evaluated and compared against customer and engineering requirements. For complex design selection, scoring matrices were used.

7.1 IMPELLER SELECTION

The impeller and shaft connection interface selection required careful evaluation and consideration of five key criteria. One of the highest ranking criteria was the ability of the impeller and shaft to survive up to 1.1N*m of torsional forces during high speed rotation up to 30,000 rpm. Further, the system needed to remain balanced while in motion.

The impeller and shaft needed to be machinable by the equipment and tooling that were available within the campus machine shop. These requirements were defined by the two-axis CNC lathe and the three-axis CNC mill. The cost at which we believed we could purchase the tooling for each design was also ranked. Lastly, robustness was defined as a criteria to account for the potential of cracking, bending, or other physical deformations.

These criteria along with the score for each of the four designs is shown in Table X.

Table X. Impeller-Shaft Connection Design Concept Scoring

Criteria | Value (1-10) | Single-Piece (0-1) | Key Slot (0-1) | Lobe (0-1) | Dowel Pin (0-1)
Torque Capability | 10 | 1 | 1 | 0.7 | 0.7
Rotational Balance Speed | 8 | 1 | 1 | 0.6 | 0.8
Machinability | 10 | 0.7 | 0.6 | 0.7 | 1
Tooling Cost | 5 | 0.8 | 0.5 | 0.8 | 0.8
Robustness | 7 | 1 | 0.9 | 0.6 | 0.6
Total | 40 | 36 | 32.8 | 27 | 31.6

The four designs were compared against the five criteria. Each criteria was given a value of importance ranging from 1-10, with 10 being very important. Each design was ranked from 0-1 and multiplied by the criteria’s ranked value. The values in the bottom row were each compared to the maximum criteria value (40) and the highest scoring design was selected. CAD illustrations for the the key slot and single-piece shaft designs are shown in Figure 1 and Figure 2.

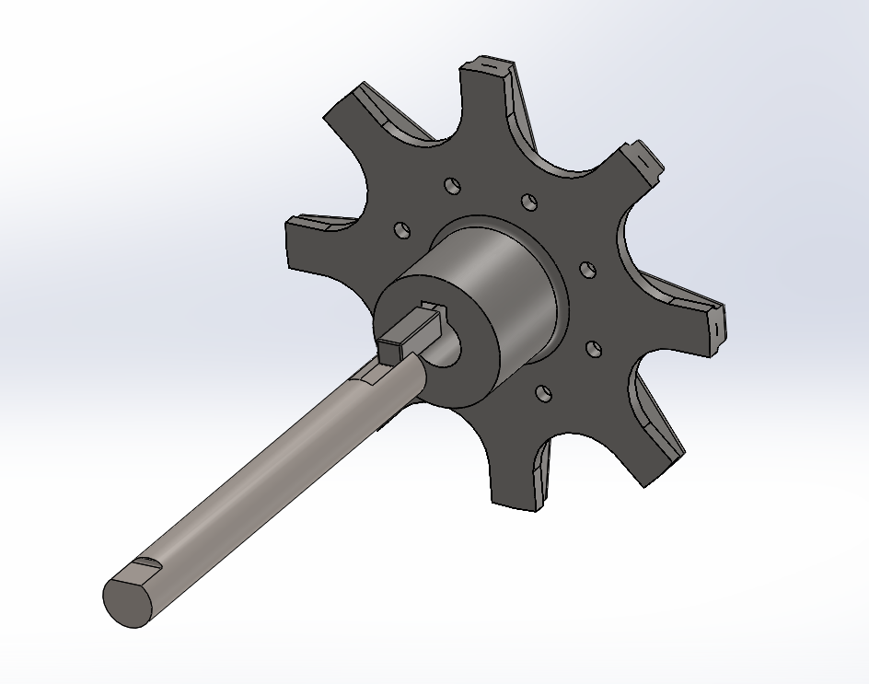
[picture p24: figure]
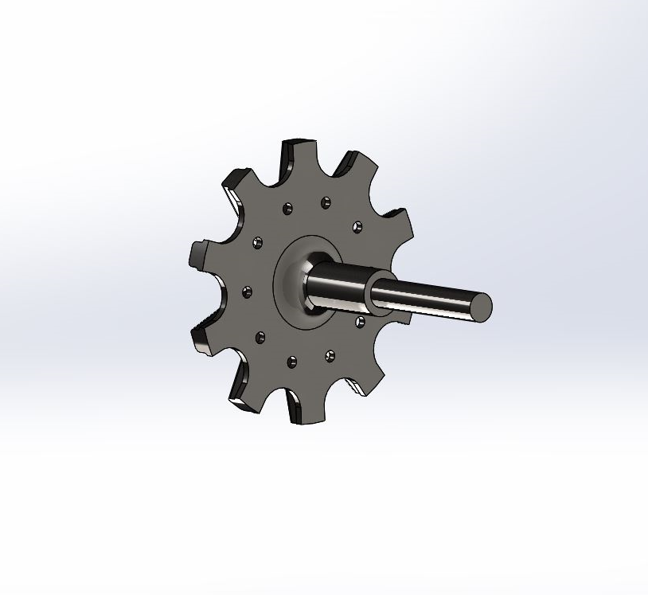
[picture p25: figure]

Figure 1. Impeller with shaft and key slot Figure 2. Impeller with single-piece shaft

The final design evaluation resulted in the selection of the single-piece shaft. It was determined that this design could be made in-house at PSU from 3” diameter, 3 ¾ long raw stock 6061-T6 aluminum. This design scored the highest against the matrix design criteria and was selected to move forward with to begin prototyping.

7.2 MOTOR SELECTION

This concept scoring method was also used when evaluating purchase of the motor. Criteria including torque, power, weight, and price were used when comparing motor specifications. Our final decision resulted in the selection of a TP Power Brushless 4070 CM Series Motor which has a common application in RC fast electric boating.

7.3 PUMP HOUSING

Following determination of impeller geometry, the team set out to select a material for the impeller of to be made out of. Primary concerns for material selection included material strength, weight, cost, and manufacturability. After careful review, the team decided to move forward with aluminum alloy 6061-T6, an alloy commonly found in aerospace applications. Due to AL 6061-T6’s relatively low cost and high machinability rating, it was an ideal candidate for prototypes. Should prototypes prove to satisfy all requirements, no additional parts would need to be manufactured since the prototypes are already made out of the design material.

8. PROGRESS ON DESIGN

After defining the qualitative criteria and selecting a design to pursue for the impeller, motor, and pump housing, we began to define the quantitative criteria.

8.1 IMPELLER

Deciding upon the final connection for the impeller and shaft proved to be one of the most challenging portions of the design. Beginning with dimensions, the quantitative criteria that were needed included impeller diameter, eye diameter, and impeller housing diameter. Considering these along with the impeller tip speed and mass flow rate, we were able to define these characteristics which are summarized in Table F.

Table F. Engineering Criterion for Impeller Characteristics

Parameter | Value
Mass Flow Rate (kg/s) | 0.93
Impeller Tip Speed (ft/s) | 211.32
Pressure Gain (psi) | 343
Impeller Diameter (in) | 2.682
Eye Diameter (in) | 0.267
Impeller Housing Diameter (in) | 3.091

The calculations for the specifications summarized in Table F. can be found in Appendix B.

8.2 MOTOR SELECTION

We determined that our motor needed to provide a minimum power output of 2.053 kW and must provide at least 0.88 N*m of torque. The calculations for determining these parameters can be found in Appendix B. We purchased our motor selection, the TP Power Brushless 4070 CM Series Motor, which provides up to 5 kW of power with a delivery of 264 amps.

8.3 PUMP HOUSING

Pump housing was machined out of plastic (UHMW) to provide a better understanding of machining operations and overall fit before machining the aluminum prototype. This also proved beneficial to tooling life and cost reduction, as UHMW material is easy to machine with minimum wear on cutting tools. Bore and depth dimensions as well as pipe thread type needed for the pipe to front housing case were finalized based on length of thread engagement calculations done during out internal search. An accurate analysis for the minimum thread engagement length resulted in a reduced overall thickness of the front housing case. The benefits of this analyses were more flexible tool cutting selection, faster machining time and weight reduction for the main housing case.

9. CONCLUSION

- Summarize the main decisions made, milestones achieved, and how close the project is to completion and relative to project plan.
- Indicate the main tasks to be done next and milestones to be achieved.
- Evaluate the current state of the product relative to the customer needs.
- State in what respects the design exceeds the needs and in what aspects the team had to make compromises regarding performance or other aspects of the design.

Be honest!

With many important smaller decisions made along the way, our biggest milestones this term were finalizing design for the impeller, the motor, and the pump housing. Pursuing a Barske impeller and a single-piece shaft connection will produce low flow, high pressure objective while also allowing for manufacturability in-house. Reducing the sections of pump housing from four sections down to two will also make a monumental difference in terms of weight reduction.

Although we are still far from completion, the rate at which we have been able to machine components for prototyping and testing has moved along quickly. We have been able to verify tool paths by machining plastic iterations of nearly all of the pump housing and have completed several impeller designs made of aluminum.

The current state of the project is near where we want it to be. Working closely with our sponsor, we have been able to communicate weekly on progress and are meeting all customer needs. Some of the bigger upcoming milestones we expect to have next term are finishing aluminum manufacturing of the pump housing to lead toward final assembly and testing. We also expect to finalize our controls and material selection for the pump components to be used in the liquid oxygen side of the system.

We have been able to exceed PSAS’s needs by having prototypes earlier than expected. Our team has shown tremendous effort in the way of producing CAD design and machining parts. Although with the great effort, we have faced the caveat of not being able to truly identify performance until testing has been completed. The only way to prove a pump’s design is to run it. We hope to begin pump testing as early as the first week of spring term.

APPENDIX B

We might need to save these for the next report…

: (

Julio’s Original Words:

Currently, we are searching for affordable cryogenic compatible pump components including seals, bearings, pressure transducers, and flow meters. Readily available cryogenic compatible components are expensive, and exceed the project’s budget. Taking cost into consideration, the team is looking into creative solutions to fulfill the system requirements. An idea under review for pressure reading currently involves using an expensive transducer connected to a standoff tube which will allow the cryogenic liquid to vaporize. In this configuration, the transducer would measure the warmer vapor pressure rather than the cooler fluid directly, in order to stay within its operating temperature range. Need to insert a source for this idea.


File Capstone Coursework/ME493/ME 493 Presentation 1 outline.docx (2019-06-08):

ME493 Presentation 1 Outline

1. Title Slide (Julio, plus all
  a. Name
  b. Sponsor
  c. Team Number
  d. Team Members
  e. Awesome Picture
2. Presentation Agenda (Julio)
3. Project Proposal (Jonas)
  a. Brief description of project assignment
  b. New PSAS Logo (in drive under Media Folder)
4. Customer Requirements (Jonas)
  a. Update to LN2 instead of LOX
5. Engineering Requirements (Jonas)
  a. Update with all current values
6. Project Progress Update
  a. Impeller machined (Jonas)
    i. Include CAD and Live images
    ii. Bring part to class?
  b. IPA casing final design (Phil)
    i. Seal selection
    ii. Bearing selection
    iii. Shaft Collar design
  c. Shaft power components selected (Julio)
    i. Measurements Project data
  d. Test Stand (Julio)
7. Gantt Chart (Phil)
  a. Update with final dates for the term
8. Current Ongoing Projects
  a. IPA case manufacturing (Jonas)
    i. Picture of profile OP from today
  b. Pump Testing (Julio)
  c. LN2 Case design (Phil)
9. Technical Writing Tips (Julio
  a. Feedback Application moving forward
10. Conclusion Slide (Phil)
  a. AWESOME PICTURE
  b. Recap goal of project
  c. Questions...

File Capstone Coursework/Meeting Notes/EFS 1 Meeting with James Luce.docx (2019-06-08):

01/22/2018

Agenda

- Introductions
- EFS 1 project takeaways
- Future iteration advice
- Impeller design
  - Vane count effect?
  - Discuss Phil/Sultzer Barske design
  - Locking Mechanism
- Control System
  - ESC communication
- LOX
  - Seals
- Shaft Design
  - Manufacturing challenges
  - Should we send out to be made?

Notes

Bearings inside the housing too big,

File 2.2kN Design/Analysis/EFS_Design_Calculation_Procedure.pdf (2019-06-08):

## Electric Feed System Pump Design Calculation Procedure

The following document outlines the theory and procedures used to calculate impeller and housing dimensions for the Portland State Aerospace Society’s Electric Feed System (EFS) for bipropellant rocket engines.

The calculations required to reach these results are based on the following inputs:

- Rmixed: The ratio of liquid oxygen to fuel
- Pp: The required pressure inside the pump chamber
- Pi
: Pressure at pump inlet
- Uss: Suction specific speed (typically between 7000-12000)
- η: Target pump efficiency
- L: Impeller hub to tip ratio
- Ψ: Stage Head Coefficient
- f: Thrust

Rocket Model

For the rocket model, a specific impulse of Isp = 221.4 [s] will be used. Then the required mass flow rate for both fluids can be found as:

m˙ T otal =

f
g · Isp

Where g is the gravitational constant. With this value, the mass flow rate required for each fluid can be calculated using the mixture ratio provided as user input.

m˙ LOX =

m˙ T otal
1 + 1 Rmixed

m˙ IP A =

m˙ T otal

1 + Rmixed

A loss factor FLoss = 1.15 is then used to calculate the pressure gain needed.

∆P = Pp × LLoss − Pi

1

Pump Design

The number of stages to be used in the pump is dependent on the pressure rise per stage, ∆Ps. This value is the maximum allowable pressure rise for a single stage, after which additional stages must be added. a value of ∆Ps = 47 [M pa] = 6817 [psi] is used. Then the number of stages, N, is found as the following (rounding up the nearest whole integer):

N =

∆P
∆Ps

Note that an inducer inlet flow coefficient, φ, is used for dimensioning purposes if an inducer is to be used in the pump design in addition to the impeller(s). This value is φ = 0.1 if an inducer is used.


The volumetric flow of the fluids is used to calculate the pump rotational speed, nRPM, and pump specific speed, ns. These values are calculated using the density of each fluid:

Q =

m˙
ρ
The required head rise, vapor pressure head, and inlet head for each fluid (in feet) can be found as:

Hp = 144 ×

∆P
ρ

Hi = 144 ×

Pi
ρ

Hv = 144 ×

Pv
ρ

The impeller tip speed, ut, gives us the tangential speed of the outermost diameter of the impeller. This value can be calculated as:

ut = φ =

r
2 · g · Hp
N
The available net pressure suction head, NP SHa is calculated as:

NP SHa = Hi − Hv

With a Thoma Parameter of τ = 2, the rotational NP SH is calculated as:

NP SHr =

NP SHa
2
Now, the rotational speed nRPM and specific speed ns can be found.

nRPM =

Uss ∗ NP SH

1
4
r
21.2 ∗

√
Q

ns =

2 · Uss
2 · π

Note: The calculated value of ns can be compared with Table 10-2 for validation.

2

Impeller Design

The calculated impeller dimensions are shown in the figure to the right. The impeller discharge diameter, Do, and eye (or inlet) diameter, Di

, are found as:

Do =

ut
2 · ns

Di =

4 ∗ Q
π · φ · nrad · (1 − L²)

1
3

Note that for Di
, n is in radians, not RPM. To find DH, calculate the following:

DH = Do · L


Based on the calculated discharge diameter, the housing diameter for the pump can be estimated as:

Dp ≈ Do · 1.152

Motor Requirements

The power required from each motor in order to drive the pumps is calculated as follows:

PReq =

m˙ · Hp
(0.738)µ

1
1000

=

m˙ · Hp
738µ

From this, the load torque can be calculated:

T = (9.5488)(1000) PReq

nRPM

= (9548.8) PReq

nRPM

3

Ideal ranges for pump specific speed ns for different impeller types


4

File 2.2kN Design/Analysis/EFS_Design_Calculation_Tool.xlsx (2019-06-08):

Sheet: Calculations
Electric Feed System
Design Calculation Tool
P. Wahl (4/23/2019)
Iteration 2 |  |  |  | Portland State Aerospace Society
 | INPUTS
 | Mixture Ratio (for mass flow) | mmix | [-] | 1.8
 | Infuser | [-] | [-] | No
 | Inlet Pressure | Pi | [psi] | 45
 | Pressure Loss (From Pintle) | PL | [psi] | 53
 | Pressure Gain | ΔP | [psi] | 343
 | Suction Sp. Speed | Uss | [-] | 7000
 | Pump Efficiency | η | [%] | 0.60
 | Impeller Hub to Tip Ratio | L | [-] | 0.3
 | Stage Head Coefficient | Ψ | [-] | 0.8
 | Thrust | f | [N] | 2200
 | Specific Impulse | Isp | [s] | 242.4
 | OUTPUTS
 | Rocket Model
SI | Total Mass Flow | ṁtotal | [kg/s] | 0.93
 | LOX Mass Flow | ṁLOX | [kg/s] | 0.59
 | IPA Mass Flow | ṁIPA | [kg/s] | 0.33
US | Total Mass Flow | ṁtotal | [lbm/s] | 2.04
 | LOX Mass Flow | ṁLOX | [lbm/s] | 1.31
 | IPA Mass Flow | ṁIPA | [lbm/s] | 0.73
 | Pump Design
 | Chamber Pressure | Pp | [psi] | 441
 | Max. Pressure Rise Per Stage | ΔPs | [psi] | 6816.786
 | Number of Stages | N | [-] | 1
 | Inducer Inlet Flow Coefficient | φ | [-] | 1.0
 | Thoma Parameter (τ ≥2 to avoid caviation) | τ | [-] | 2
 |  |  |  | LOX | IPA
 | Volumentric Flow | Q | [GPM] | 8.262 | 6.638
 |  |  | [ft³/s] | 0.018 | 0.015
 | Required Head Rise | Hp | [ft] | 693.41 | 1002.77
 | Inlet Head | Hi | [ft] | 45.54 | 65.86 | Hi for LOX is cut in half but not for IPA…if it were as well, required RPM would drop significantly. Need to find theory for this calculation
 | Vapor Pressure Head | Hv | [ft] | 2.35 | 3.75
 | Impeller Tip Speed | ut | [ft/s] | 211.32 | 254.12
 | Available NPSH | NPSHa | [-] | 43.20 | 62.11
 | Rotational NPSH | NPSHr | [-] | 21.60 | 31.06
 | Pump Specific Speed | ns | [RPM] | 4956.05 | 4934.84
 |  |  | [rad/s] | 519.00 | 516.78
 | Impeller Design
 |  |  |  | LOX | IPA
 | Discharge Diameter | Do | [in] | 2.443 | 2.950
 | Inlet Diameter | Di | [in] | 0.259 | 0.212
 | Impeller Hub Diameter | DH | [in] | 0.733 | 0.885
 | Impeller Housing Diameter | Dp | [in] | 2.815 | 3.400
 | Motor Requirements
 |  |  |  | LOX | IPA
 | Required Power | Preq | [kW] | 2.053 | 1.650
 | Load Torque | T | [N٠m] | 0.80 | 0.55
 | Rotational Speed | nRPM | [RPM] | 24382.05 | 35718.73
 |  |  | [rad/s] | 2553.28 | 3740.46
References:
[1] I. Karassik, Pump Handbook (4th Ed.)

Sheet: General Data
Fluid_Type |  | Yes_or_No |  | Grav Constant | 9.81 |  | Uss | 7000
Liquid Oxygen |  | No |  | US Grav Const | 32.2
Ethanol |  | Yes |  | Gas Constant | 8.3145
Fluid | Density [kg/m³] | Density [lb/ft³] | Operating Pv [Pa] | Operating Pv [psi] | Temperature [K] | Specific Heat (Liquid) | Specific Heat (Vapor) | Vaporization T [K] | Specific Gas Constant | Vap. Heat [J/kg]
Liquid Oxygen | 1141 | 71.230 | 8000 | 2.346 | 90.2 | 1700 | 910 | 90.2 | 259.84 | 213050
Ethanol | 789 | 49.256 | 8840 | 3.748 | 293 | 435.725 | 1750 | 355.8 | 138.34 | 2211.68
Water | 1000 | 62.428
Impeller Properties |  |  |  | Temperatures
Specific Heat | [J/kg-K] | 502.416 |  | Room T [C] | 70
Mass | [kg] | 0.148265738 |  | Motor T [C] | 100
MMOI | [kg/m²] | 7.2170791e-05 |  | LOX T [C] | -190
Volume | [in³] | 1.1675

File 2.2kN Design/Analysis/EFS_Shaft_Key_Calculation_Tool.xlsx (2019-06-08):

Electric Feed System
Shaft Key Calculation Tool
 |  |  |  | Portland State Aerospace Society
 | INPUTS
 | Material | [-] | [-] | 304 Stainless
 | Shaft Diameter | d | [mm] | 10.00
 | Key Length | L | [mm] | 20.00
 | Key Width | b | [mm] | 4.00
 | Key Height | h | [mm] | 4.00
 | Torque | T | [N٠m] | 1.10
 | Keyway Shaft Depth | t1 | [mm] | 2.50
 | Keyway Hub Depth | t2 | [mm] | 1.80
 | OUTPUTS
 | Shear Force | Fs | [N] | 220.00
 | Shear Stress on Key | V | [MPa] | 2.75
 | Nominal Torsional Stress | τ | [MPa] | 13.28

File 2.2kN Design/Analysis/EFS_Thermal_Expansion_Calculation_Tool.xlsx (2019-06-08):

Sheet: Design Calculations
Electric Feed System
Impeller Thermal Expansion Calculation Tool
P. Wahl (5/06/2019)
Iteration 1 |  |  | Portland State Aerospace Society
INSTRUCTIONS
Enter the desired dimension for the labeled distances in the figures to the right (column I). The change in length/diameter is calculated based on thermal expansion theory and experiementally derived ajustment factors (see "Measured vs. Theoretical" sheet). This is used to provide the final machined dimensions required.
INPUTS
Material |  | [-] | [-] | Aluminum
Ambient Temperature |  | Ta | [°C] | 20
Fluid Temperature |  | Tc | [°C] | -196
IMPELLER
COOLED | Outer Diameter | A | [in] | 2.443
 | Shaft Seal Diameter | B | [in] | 0.500
 | Shaft Coupler Diameter | C | [in] | 0.314
 | Shaft Length | D | [in] | 3.247
CHANGE | Outer Diameter | ΔA | [in] | -0.0137
 | Shaft Seal Diameter | ΔB | [in] | -0.0039
 | Shaft Coupler Diameter | ΔC | [in] | -0.0030
 | Shaft Length | ΔD | [in] | -0.0178
DESIGN | Outer Diameter | A | [in] | 2.4567
 | Shaft Seal Diameter | B | [in] | 0.5040
 | Shaft Coupler Diameter | C | [in] | 0.3170
 | Shaft Length | D | [in] | 3.2648
BEARING COLLAR
COOLED | Bearing Diameter | A | [in] | 0.995
CHANGE | Bearing Diameter | ΔA | [in] | -0.0064
DESIGN | Bearing Diameter | A | [in] | 1.0014
CASE 1
COOLED | Impeller Seat Diameter | A | [in] | 3.450
 | Impeller Shaft Bore Diameter | B | [in] | 0.931
 | Seal Retaining Ring Diameter | C | [in] | 1.537
CHANGE | Impeller Seat Diameter | ΔA | [in] | -0.0188
 | Impeller Shaft Bore Diameter | ΔB | [in] | -0.0061
 | Seal Retaining Ring Diameter | ΔC | [in] | -0.0092
DESIGN | Impeller Seat Diameter | A | [in] | 3.4690
 | Impeller Shaft Bore Diameter | B | [in] | 0.9369
 | Seal Retaining Ring Diameter | C | [in] | 1.5465
CASE 2
COOLED | Housing Internal Diameter | A | [in] | 3.450
 | Housing Depth | B | [in] | 1.167
CHANGE | Housing Internal Diameter | ΔA | [in] | -0.01883
 | Housing Depth | ΔB | [in] | -0.00730
DESIGN | Housing Internal Diameter | A | [in] | 3.4690
 | Housing Depth | B | [in] | 1.1743
SEAL RETAINING RING
COOLED | Seal Seat Diameter | A | [in] | 0.994
CHANGE | Seal Seat Diameter | ΔA | [in] | -0.0064
DESIGN | Seal Seat Diameter | A | [in] | 1.0007
BEARING PLATE
COOLED | Bearing Outer Diameter | A | [in] | 1.969
CHANGE | Bearing Outer Diameter | ΔA | [in] | -0.01135
DESIGN | Bearing Outer Diameter | A | [in] | 1.9807

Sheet: Theory Calculations
Electric Feed System
Impeller Thermal Expansion Calculation Tool
P. Wahl (5/06/2019)
Iteration 1 |  |  | Portland State Aerospace Society
THEORY
INPUTS
Material |  | [-] | [-] | Aluminum
Ambient Temperature |  | Ta | [°C] | 20
Fluid Temperature |  | Tc | [°C] | -196
IMPELLER
INITIAL | Outer Diameter | A | [in] | 2.982
 | Shaft Seal Diameter | B | [in] | 0.500
 | Shaft Coupler Diameter | C | [in] | 0.314
 | Shaft Length | D | [in] | 3.247
CHANGE | Outer Diameter | ΔA | [in] | -0.0149
 | Shaft Seal Diameter | ΔB | [in] | -0.0025
 | Shaft Coupler Diameter | ΔC | [in] | -0.0016
 | Shaft Length | ΔD | [in] | -0.0163
COOLED | Outer Diameter | A | [in] | 2.9669
 | Shaft Seal Diameter | B | [in] | 0.4976
 | Shaft Coupler Diameter | C | [in] | 0.3124
 | Shaft Length | D | [in] | 3.2307
BEARING COLLAR
INITIAL | Bearing Diameter | A | [in] | 0.995
CHANGE | Bearing Diameter | ΔA | [in] | -0.0050
COOLED | Bearing Diameter | A | [in] | 0.9900
CASE 1
INITIAL | Impeller Seat Diameter | A | [in] | 3.450
 | Impeller Shaft Bore Diameter | B | [in] | 0.931
 | Seal Retaining Ring Diameter | C | [in] | 1.537
CHANGE | Impeller Seat Diameter | ΔA | [in] | -0.0173
 | Impeller Shaft Bore Diameter | ΔB | [in] | -0.0047
 | Seal Retaining Ring Diameter | ΔC | [in] | -0.0077
COOLED | Impeller Seat Diameter | A | [in] | 3.4328
 | Impeller Shaft Bore Diameter | B | [in] | 0.9261
 | Seal Retaining Ring Diameter | C | [in] | 1.5296
CASE 2
INITIAL | Housing Internal Diameter | A | [in] | 3.450
 | Housing Depth | B | [in] | 1.167
CHANGE | Housing Internal Diameter | ΔA | [in] | -0.0173
 | Housing Depth | ΔB | [in] | -0.0058
COOLED | Housing Internal Diameter | A | [in] | 3.4328
 | Housing Depth | B | [in] | 1.1612
SEAL RETAINING RING
INITIAL | Seal Seat Diameter | A | [in] | 0.994
CHANGE | Seal Seat Diameter | ΔA | [in] | -0.0050
COOLED | Seal Seat Diameter | A | [in] | 0.9893
BEARING PLATE
INITIAL | Bearing Outer Diameter | A | [in] | 1.969
CHANGE | Bearing Outer Diameter | ΔA | [in] | -0.0099
COOLED | Bearing Outer Diameter | A | [in] | 1.9594

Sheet: Curve Generation
Component |  | Measurement | Unit | Initial Length | Length @Cryogenic Temperatures
 |  |  |  |  | Theoretical | Measured |  | % Difference
 | Shaft Seal Diameter | B | [in] | 0.5001 | 0.4976 | 0.4984 |  | 0.1617
 | Shaft Length | D | [in] | 3.2470 | 3.2296 | 3.2400 |  | 0.3199
COLLAR | Bearing Diameter | A | [in] | 0.9950 | 0.9900 | 0.9920 |  | 0.1969
CASE 1 | Impeller Seat Diameter | A | [in] | 3.4500 | 3.4328 | 3.4400 |  | 0.2081
 | Impeller Shaft Bore Diameter | B | [in] | 0.9310 | 0.9261 | 0.9287 |  | 0.2761
CASE 2 | Housing Internal Diameter | A | [in] | 3.4500 | 3.4328 | 3.4408 |  | 0.2313
 | Housing Depth | B | [in] | 1.1670 | 1.1612 | 1.1590 |  | 0.1898
S.R. Ring | Seal Seat Diameter | A | [in] | 0.9940 | 0.9893 | 0.9919 |  | 0.2570
BRG. PLATE | Bearing Outer Diameter | A | [in] | 1.9690 | 1.9594 | 1.9632 |  | 0.1920
 |  |  |  |  |  |  | Average % Difference: | 0.2259
 |  |  |  |  |  |  |  |  | Theoretical | Measured
 |  |  |  |  |  |  |  |  | 0.4976 | 0.4984
 |  |  |  |  |  |  |  |  | 3.2296 | 3.2400
 |  |  |  |  |  |  |  |  | 0.9900 | 0.9920
 |  |  |  |  |  |  |  |  | 3.4328 | 3.4400
 |  |  |  |  |  |  |  |  | 0.9261 | 0.9287
 |  |  |  |  |  |  |  |  | 3.4328 | 3.4408
 |  |  |  |  |  |  |  |  | 1.1612 | 1.1590
 |  |  |  |  |  |  |  |  | 0.9893 | 0.9919
 |  |  |  |  |  |  |  |  | 1.9594 | 1.9632

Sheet: General Data
Aluminum Coefficient of Thermal Expansion
α | 2.32e-05

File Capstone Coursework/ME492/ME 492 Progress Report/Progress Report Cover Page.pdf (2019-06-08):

# ME 492 | Winter 2019

# Progress Report


# Flight Ready Electric Feed System

Sponsored by Portland State Aerospace Society (PSAS)

TEAM MEMBERS:

Julio Garcia
Philip Wahl
Jonas Mendoza
Nick Sheldon
Henry Ju
Shayli Elrod

ACADEMIC ADVISER:
Baldur Steingrimsson

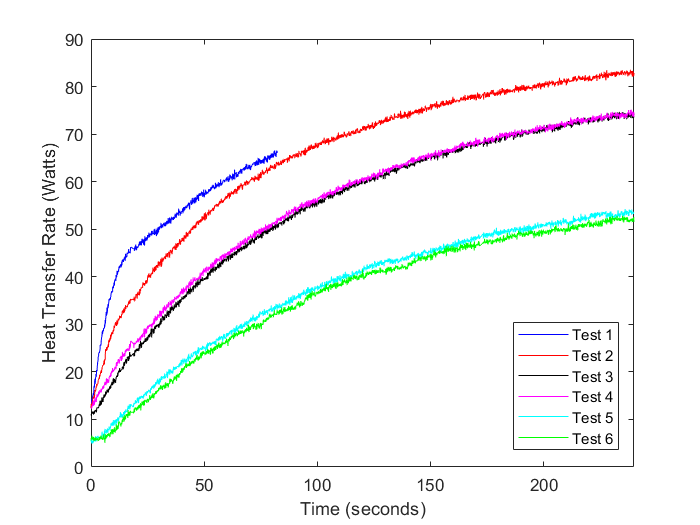
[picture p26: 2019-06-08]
Capstone Coursework/ME492/ME 411 Project/Final Report/Figures/HeatTransferRates.png

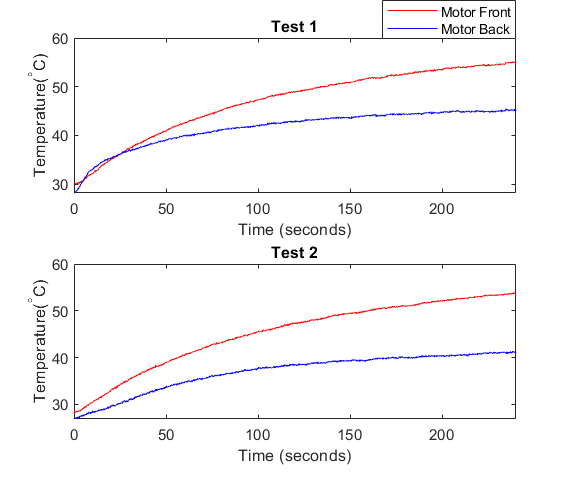
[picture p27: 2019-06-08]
Capstone Coursework/ME492/ME 411 Project/Final Report/Figures/BackJacketPlot.png

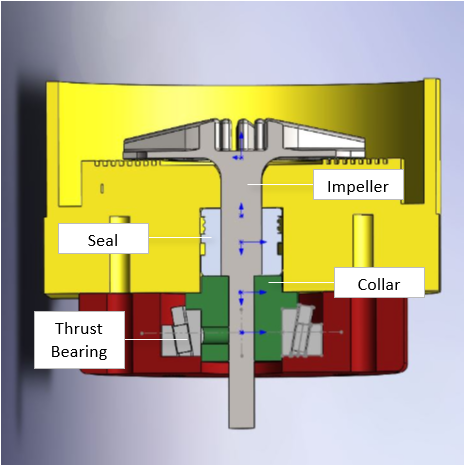
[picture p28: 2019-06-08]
Capstone Coursework/ME492/ME 411 Project/Final Report/Figures/Apparatus_XSection.png

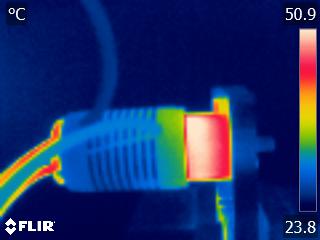
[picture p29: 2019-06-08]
Capstone Coursework/ME492/ME 411 Project/Final Report/Figures/CoolingJacketRear.jpg

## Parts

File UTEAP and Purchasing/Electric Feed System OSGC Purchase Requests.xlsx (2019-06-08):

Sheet: EFS Budget
Item | Description | Vendor | Award Amount | 1.5:1 Cost Share
Cost Share
In-Kind AY effort | Dr. Mark Weislogel donating his time working as PI on Project | Portland State University |  | $6556 | this is inclusive of 0.29 months of effort + fringe (OPE)
Award Budget
304 SS Steel | Raw material used to machine pump housing | McMaster-Carr | $800
Tooling | Pump House machine tooling | Western Precision Products Inc | $1400
6061 Aluminum | Raw Material to create EFS Airframe Structure | McMaster-Carr | $200
304 SS Steel | ¼” x 24” TGP Precision Shaft | Metals Depot | $10
Impeller | Rotational Impellers for propellants | Shapeways | $200
ISO Plumbing | Various plumbing fittings for alcohol | Home Depot | $100
LOX Plumbing | Various LOX compatible fittings | AcmeCryo | $300
Aluminum Piping | ½” Aluminum piping for plumbing | Metals Depot | $100
Seals | Metal C-Ring Internal Pressure Face Seals | Parker | $30
Liquid Oxygen | 40 Gallons of LOX for testing | Airgas | $200
Liquid Nitrogen | 40 Gallons of LN for cryo testing | Airgas | $200
Electric Motor | Brushless Motor for shaft drive | Hobbyking | $150
Heat Sink | Heat Sink for Brushless motor | Amazon | $25
Arduino | Arduino to Controlling pump | Amazon | $50
Sensing Equipment | Pressure Transducers and flow meters for fluid monitoring | Omega | $500
Total Direct Costs |  |  | $4265 | $6556
Total Indirect Costs |  | 48.50% | $2068.525 | $3179.66
Total Project Costs |  |  | $6333.525 | $9735.66 | required per federally negoatiated agreement - allowed per OSGC - 48.5% of adirect costs
Cost Share Ratio | 1.537

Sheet: Financial Expenditure 3_22_2019
PI: | Mark Weislogel |  | Financial Expenditure Report
Sponsor: | OSU/NASA |  | Reporting thru | 2019-03-22
Title: | Oregon/NASA Space Grant Program - Feed System | Student lead = | Timothy Finn
Index: | 244812
Start Date: | 2018-11-18 | NCE ancicipated thru 6/29/19
End Date: | 2019-04-22
F&A Rate: | 48.50%
 |  |  | Thru 03/22/2019 | Encumbrances |  | % Balance
Account | Description | Budget | Expenditures |  | Balance | Available
20001 | Materials & Supplies | 4265.00 | - |  | 4265.00
20103 | Laboratory Supplies | - | 2207.38 | 203.74 | -2411.12
20200 | minor equipment |  |  | - | -
20204 | other IT related peripherals |  | - |  | -
20219 | Inventoried Equipment | - |  |  | -
20106 | Books Publication & Other Ref. Mat. | - | - |  | -
24606 | Printing & Publishing | - |  |  | -
24999 | Misc. Fees & Services | - |  |  | -
25010 | Compressed Gases | - |  |  | -
28601 | Conference Registration Fees | - |  |  | -
28901 | Dues & Memberships | - |  |  | -
28999 | Misc. Services & Supplies | - |  |  | -
 | Subtotal Services & Supplies | $4265.00 | $2207.38 | $203.74 | $1853.88 | 43%
 | Total Direct Costs | $4265.00 | $2207.38 | $203.74 | $1853.88 | 43%
70005 | F & A Cost (formerly Indirect) | $2069.00 | $1070.57 | $98.81 | $899.62 | 43%
 | Total Operating Costs | $6334.00 | $3277.95 | $302.55 | $2753.50 | 43% | Check for Balance Total
 |  |  |  | DC available | 1854.21 |  | $2753.50 | Correct!
Encumbrances
10102
10501 |  | $ -
 | Subtotal Salaries & Wages | $ -
109XX |  | $ -
 | Subtotal Fringe & Remission | $ -
20103
20103 | pending PI approval for order (various vendors) | $155.74 | JZ 3/29/19
20103 | MSC Direct | $48.00
20103 |  |  | JZ 3/29/19 - please update once purchse is made
20103
 | Subtotal Materials & Supplies | $203.74
 | Total | $203.74

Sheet: Updated Funds 4_30_2019
Total Direct Costs Available | Billed as of 3-29-2019 | Remaining as of 3-29-2019 | Total Reimbursement Pending | Spending between 3-29-2019 and 4-30-2019 | Remaining as of 4-30-2019
$4265.00 | -$2411.12 | $1853.88 | -$604.59 | -$333.32 | $915.97
Reimbursement Pending | Reimbursement ID
-132.23 | Jonas
-38.82 | Julio
-82.28 | Julio
-49.58 | Julio
-49.98 | Julio
-25.4 | Julio
-8.99 | Julio
-217.31 | Tim
-604.59

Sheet: Item Requests
EFS Team Initial Item Requests
Item | Part Name | Part Number | Unit Price | Quantity | Vendor | Description of Item | Notes (comments, weblink to item, etc.) |  | Who Needs? | Date Added | Date Ordered | Date Received
1 | LabJack | U6 | 319 | 2 |  | LabJack | https://labjack.com/products/u6 |  | Julio | 2019-01-24 | 2019-01-30 | 2019-02-06
2 | CB37 |  | 46 | 2 |  | LabJack | https://labjack.com/accessories/cb37-terminal-board |  | Julio | 2019-01-24 | 2019-01-30 | 2019-02-06
3 | CB15 |  | 33 | 2 |  | LabJack | https://labjack.com/accessories/cb15-terminal-board |  | Julio | 2019-01-24 | 2019-01-30 | 2019-02-06
4 | Pressure Transducer | MSP 300 | 55.8 | 4 |  | Mouser Electronics | https://www.mouser.com/ProductDetail/Measurement-Specialties/M3021-000005-05KPG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 |  | Julio | 2019-01-24 | 2019-01-30 | 2019-02-05
5 | Aluminum stock | 8975K286 | 124.74 | 1 | McMaster | 3" x 5" x 12" (inches) aluminum bar stock | https://www.mcmaster.com/8975k286 |  | Jonas | 2019-02-04 | 2019-02-12 | 2019-02-14
6 | Milling-Machine Vise Jaws | 1005N24 | 25.58 | 1 pair | McMaster | Machineable, 6" Wide x 2" High | https://www.mcmaster.com/1005n24 |  | Jonas | 2019-02-04 | 2019-02-12 | 2019-02-14
7 | Aluminum Bar Stock 6061-T651 | 1103 | 45.62 | 2 | Online Metals | Aluminum 6061-T6511 3" Round, Extruded Bar Stock. "Random Length (10" - 12")" | https://onlinemetals.com/merchant.cfm?pid=1103&step=4&showunits=inches&id=195&top_cat=60 | Use code "DCEDU" for educator / student discount. UPS Ground Shipping is alright | Nick | 2019-02-07 | 2019-02-12
8 | Aluminum Bare Plate 6061 T651 | 4533 | 20.48 | 2 | Online Metals | Please create a custom size at the bottom of the webpage for a 1-inch thick 4"x4" sheet. Each plate costs $20.48 | https://www.onlinemetals.com/merchant.cfm?pid=4533&step=4&showunits=inches&id=76&top_cat=60 |  | Shayli | 2019-02-07 | 2019-02-12
9 | TP Power Brushless 4070 CM | tp-4070-cm | 188.89 | 1 | Offshoreelectrics | Electric motor for powering IPA pump | https://www.offshoreelectrics.com/proddetail.php?prod=tp-4070-cm |  | Julio | 2019-02-18 | 2019-02-19 | 2019-03-01
10 | Swordfish X+ 200A ESC | hef-HBX1200L | 179.95 | 1 | Offshoreelectrics | Electronic Speed Controller for IPA motor | https://www.offshoreelectrics.com/proddetail.php?prod=hef-HBX1200L |  | Julio | 2019-02-18 | 2019-02-19 | 2019-03-01
11 | Revolectrix LiPo Pack | ev-ys5000 - 6s | 114.99 | 3 | Offshoreelectrics | Battery pack for EFS | https://www.offshoreelectrics.com/proddetail.php?prod=rev-ys5000 |  | Julio | 2019-02-18 | 2019-02-19 | 2019-03-01
12 | ULTRAPOWER Dual Battery Charger | ker-10685 | 119.95 | 1 | Offshoreelectrics | Battery Charger for EFS Battery Pack | https://www.offshoreelectrics.com/proddetail.php?prod=ker-10685 |  | Julio | 2019-02-18 | 2019-02-19 | 2019-03-01
13 | Tapered Roller Bearing | 5709K42 | 38.64 | 2 | McMaster | IPA pump bearings | https://www.mcmaster.com/5709k42 |  | Julio | 2019-02-28 | 2019-02-28 | 2019-04-02
14 | 1/2" Flowserve shaft seal | 5NC02 | 18.49 | 3 | Grainger | IPA pump seals | https://www.grainger.com/product/FLOWSERVE-1-2-Replacement-Pump-Shaft-5NC02 |  | Julio | 2019-02-28 | 2019-02-28 | 2019-04-02
15 | HATCHBOX 3D PLA-1KG3.00-BLK PLA 3D Printer Filament, Dimensional Accuracy +/- 0.03 mm, 1 kg Spool, 3.00 mm, Black | 3D PLA-1KG3.00-SLV | 22.99 | 1 | By HATCHBOX on Amazon.com | 3D Printer Filament | https://www.amazon.com/dp/B019EFB79E/ref=twister_B01FKESAMA?_encoding=UTF8&th=1 |  | Nick | 2019-02-28 | 2019-02-28 | 2019-04-02
16 | Kennametal - DNMG332 MP Grade KC5010 Carbide Turning Insert | 6463731 | 24 | 1 | MSC Direct | CNC Turning Insert | https://www.mscdirect.com/product/details/06463731 |  | Nick | 2019-03-02 | 2019-03-04 | 2019-04-02
17 | Kennametal - DNMG331 FF Grade KC5010 Carbide Turning Insert | 2292282 | 24 | 1 | MSC Direct | CNC Turning Insert | https://www.mscdirect.com/product/details/02292282 |  | Nick | 2019-03-02 | 2019-03-04 | 2019-04-02
18 | End Mills - one main order, several items. see order | B576089 | 217.31 | 1 | Mesher tool | This order contains 9 different items. SEE attached order. PLEASE CALL OR EMAIL DARREN AT MESHER TOOL, AND PLACE ORDER FROM Order Number : B576089 | https://docs.google.com/spreadsheets/d/1V93y9MX_VvAHEh94AOJ8yqf05BlQjTOLXBTAKcgp24k/edit |  | Jonas | 2019-03-26 |  | Received
19 | Aluminum bar stock 6061 | 8975K631 | 75.61 | 1 | McMaster | 5 inches wide, 2 inches thick, 12 inches long | https://www.mcmaster.com/8975k631 |  | Jonas | 2019-04-02 |  | Received
20 | Aluminum bar stock 6061 | 9418T159 | 134.74 | 1 | McMaster | 5 inches wide, 3 inches thick, 12 inches long | https://www.mcmaster.com/9418T159 |  | Jonas | 2019-04-02 |  | Received
21 | 4-40 Socket Head Screws | 90128A113 | 4.55 | 1 | McMaster | Zinc-Plated Alloy Steel Socket Head Screw, 4-40 Thread Size, 3/4" Long | https://www.mcmaster.com/standard-socket-head-screws |  | Nick | 2019-04-20 |  | Received
22 | Black-Oxide Alloy Steel Socket Head Screw | 91251A540 | 7.86 | 1 | McMaster | 1/4"-20 Thread Size, 3/4" Long | https://www.mcmaster.com/91251a540 |  |  |  |  | Received
23 | Alloy Steel Shoulder Screw | 91259A101 | 3.91 | 16 | McMaster | 1/4" Shoulder Diameter, 3-1/4" Shoulder Length, 10-24 Thread | https://www.mcmaster.com/91259a101 |  |  |  |  | Received
24 | Shaft Coupler | NA | 11.4 | 2 | Amazon | 8mm Shaft Coupler | https://www.amazon.com/uxcell-Coupling-Diameter-Aluminum-Connector/dp/B06X9WVYLF?th=1 |  | Julio | 2019-04-24 | 2019-05-02 | Received
25 | Ceramic Bearing | 51104 TP ZRO2 LD | 84.5 | 1 | Boca Bearing | Ceramic bearing (Note, you will need to call the vendor to order) | http://www.bocabearings.com/ | (800)-332-3256 |  |  | 2019-05-02 | Received
26 | Swordfish X+ 200A ESC | hef-HBX1200L | 179.95 | 1 | Offshoreelectrics | Electronic Speed Controller for IPA motor | https://www.offshoreelectrics.com/proddetail.php?prod=hef-HBX1200L |  | Julio | 2019-05-01 | 2019-05-02 | Received
27 | Various Aluminum Bar Stock, cut to size | Quote #: 1075350 | 145.88 | 1 | Metal Supermarkets | I have already called the vendor and arranged a quote. All that needs to happen is call and reference the quote number. Payment can be made over the phone. Order includes the following Aluminum 6061 bars / plates: - 2" x 5" x 12" bar - 1.5" x 5" x 12" bar - 10" x 15" x 1/8" plate - 6.5" x 15" x 1/8" plate | Call Metal Supermarkets, Portland location, at phone number 503-258-1151 |  | Nick | 2019-05-01 | 2019-05-02 | Received
26 | Swordfish X+ 200A ESC | hef-HBX1200L | 159.95 | 1 | Offshoreelectrics | Electronic Speed Controller for IPA motor | https://www.offshoreelectrics.com/proddetail.php?prod=hef-HBX1220L |  | Julio | 2019-05-16 | 2019-05-16
29 | Case 2 | 1Z57S40G | 422.5 | 1 | 3D HUBS | Front case for LOX Pump | https://www.3dhubs.com/manufacture/payment/quote/4f50c46a-88b4-47dd-b5a1-eb10f61c494c |  | Jonas | 2019-05-16 | 2019-05-16
30 | PTFE Rod 7/8" Diameter | 8546K25 | 13.6 | 1 | McMaster | Raw material for LOX pump seal | https://www.mcmaster.com/catalog/125/3770 |  | Nick | 2019-05-22
31 | PTFE Rod 1-1/4" Diameter | 8546K17 | 25.18 | 1 | MaMaster | Raw material for Lox seal / bearing collar | https://www.mcmaster.com/catalog/125/3770 |  | Nick | 2019-05-22
32 | Various Aluminum Plates, cut to size | Quote #: 1077798 | 28.07 | 1 | Metal Supermarkets | I have already called the vendor and arranged a quote. All that needs to happen is call and reference the quote number. Payment can be made over the phone. Order includes the following Aluminum 6061 plates: - 10" x 15" x 1/8" plate - 6.5" x 15" x 1/8" plate | Call Metal Supermarkets, Portland location, at phone number 503-258-1151 |  | Nick | 2019-05-22
 |  |  | 3898.7 | 2923.57

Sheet: Date 1-30-2019
UTEAP DRA Purchasing Spreadsheet (TEMPLATE)
* COPY this template into your own UTEAP folder, fill out (new sheet for each purchase request), and send to PI with mcecsdra@pdx.edu Cc'ed
How the parts listed below will be used for the project (one sentence): |  |  |  |  |  | These items will help us continue design work on the pump for the Electric Feed System
Item | Part Name | Part Number | Unit Price | Quantity | Total Price | Unit of item (e.g. each pack, case, etc.) | Vendor | Description of Item | Notes (comments, weblink to item, etc.)
1 | U6 Series | U6 | 319 | 2 | 638 | Each | LabJack | USB multifunction DAQ device with 14 analog inputs (16- to 18- bit), 2 analog outputs (12-bit), 20 digital I/O, 2 counters, and 4 timers. | USB used for data aquisition for the Electric Feed System | https://labjack.com/products/u6
2 | CB37 Terminal Board | CB37 | 46 | 2 | 92 | Each | LabJack | Provides convenient screw terminals for the DB37 connector on the LabJack U6, UE9, and T7. | Terminal Board used with the U6 Series DAQ | https://labjack.com/accessories/cb37-terminal-board
3 | CB15 Terminal Board | CB15 | 33 | 2 | 66 | Each | LabJack | Provides convenient screw terminals for the 12 digital I/O lines on the DB15 connector of compatible LabJack devices. | Terminal Board used with the U6 Series DAQ | https://labjack.com/accessories/cb15-terminal-board
4 | Pressure Transducer | M3021-000005-05KPG | 55.8 | 4 | 223.2 | Each | Mouser Electronics | Industrial Pressure Sensors PRESS XDCR MSP-300-05K-P-2-N-1 | Pressure Sensor required for Electric Feed System | https://www.mouser.com/ProductDetail/Measurement-Specialties/M3021-000005-05KPG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
5 |  |  |  |  | 0
6 |  |  |  |  | 0
7 |  |  |  |  | 0
8 |  |  |  |  | 0
9 |  |  |  |  | 0
10 |  |  |  |  | 0
 |  |  | Order Total |  | 1019.2
*items to remember:
please give us time to purchase - same day requests may not be possible to fulfill
please consider shipping time - same day receipt of item is not possible and rush shipping (overnight or 2-day) should be avoided (as stewards of federal funds, we need to spend them as frugally and responsibly as possible)
if possible, please lump orders from the same vendor together (this will save on shipping and workload)
if possible, please keep overall orders to 10 items or less
If you receive quotes, please send to mcecsdra@pdx.edu for review - shipping address on quotes should be as follows: |  |  |  |  |  |  | SHIP-TO: Helen Frey Portland State University College of Engineering 1930 SW 4th Avenue, Ste 500L Portland, OR 97201 c 503 703 1157 frey@pdx.edu

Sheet: Date 2-11-2019
UTEAP DRA Purchasing Spreadsheet (TEMPLATE)
* COPY this template into your own UTEAP folder, fill out (new sheet for each purchase request), and send to PI with mcecsdra@pdx.edu Cc'ed
How the parts listed below will be used for the project (one sentence): |  |  |  |  |  | These items will help us continue design work on the pump for the Electric Feed System
Item | Part Name | Part Number | Unit Price | Quantity | Total Price | Unit of item (e.g. each pack, case, etc.) | Vendor | Description of Item | Notes (comments, weblink to item, etc.)
1 | Aluminum stock | 8975K286 | 124.74 | 1 | 124.74 | Each | McMaster | 3" x 5" x 12" (inches) aluminum bar stock | Aluminum bar used for fabrication of test structure | https://www.mcmaster.com/8975k286
2 | Milling-Machine Vise Jaws | 1005N24 | 25.58 | 1 | 25.58 | Pairs | McMaster | Machineable, 6" Wide x 2" High | Aluminum bar used for fabrication of test structure | https://www.mcmaster.com/1005n24
3 | Aluminum Bar Stock 6061-T651 | 1103 | 45.62 | 2 | 91.24 | Each | Online Metals | Aluminum 6061-T6511 3" Round, Extruded Bar Stock. "Random Length (10" - 12")" | Use code "DCEDU" for educator / student discount. UPS Ground Shipping is alright | https://onlinemetals.com/merchant.cfm?pid=1103&step=4&showunits=inches&id=195&top_cat=60
4 | Aluminum Bare Plate 6061 T651 | 4533 | 20.48 | 2 | 40.96 | Each | Online Metals | Please create a custom size at the bottom of the webpage for a 1-inch thick 4"x4" sheet. Each plate costs $20.48 | Aluminum plate used for fabrication of test structure | https://www.onlinemetals.com/merchant.cfm?pid=4533&step=4&showunits=inches&id=76&top_cat=60
5 |  |  |  |  | 0
6 |  |  |  |  | 0
7 |  |  |  |  | 0
8 |  |  |  |  | 0
9 |  |  |  |  | 0
10 |  |  |  |  | 0
 |  |  | Order Total |  | 282.52
*items to remember:
please give us time to purchase - same day requests may not be possible to fulfill
please consider shipping time - same day receipt of item is not possible and rush shipping (overnight or 2-day) should be avoided (as stewards of federal funds, we need to spend them as frugally and responsibly as possible)
if possible, please lump orders from the same vendor together (this will save on shipping and workload)
if possible, please keep overall orders to 10 items or less
If you receive quotes, please send to mcecsdra@pdx.edu for review - shipping address on quotes should be as follows: |  |  |  |  |  |  | SHIP-TO: Helen Frey Portland State University College of Engineering 1930 SW 4th Avenue, Ste 500L Portland, OR 97201 c 503 703 1157 frey@pdx.edu

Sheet: Date 2-19-2019
UTEAP DRA Purchasing Spreadsheet (TEMPLATE)
* COPY this template into your own UTEAP folder, fill out (new sheet for each purchase request), and send to PI with mcecsdra@pdx.edu Cc'ed
How the parts listed below will be used for the project (one sentence): |  |  |  |  |  | These items will help us continue design work on the pump for the Electric Feed System
Item | Part Name | Part Number | Unit Price | Quantity | Total Price | Unit of item (e.g. each pack, case, etc.) | Vendor | Description of Item | Notes (comments, weblink to item, etc.)
1 | TP Power Brushless 4070 CM | tp-4070-cm | 188.89 | 1 | 188.89 | Each | Offshoreelectrics | Electric motor for powering IPA pump | Motor for Electric Feed System | https://www.offshoreelectrics.com/proddetail.php?prod=tp-4070-cm
2 | Swordfish X+ 200A ESC | hef-HBX1200L | 179.95 | 1 | 179.95 | Each | Offshoreelectrics | Electronic Speed Controller for IPA motor | Speed controller for Electric Feed System | https://www.offshoreelectrics.com/proddetail.php?prod=hef-HBX1200L
3 | Revolectrix LiPo Pack | ev-ys5000 - 6s | 114.99 | 3 | 344.97 | Each | Offshoreelectrics | Battery pack for EFS | Battery for Electric Feed System | https://www.offshoreelectrics.com/proddetail.php?prod=rev-ys5000
4 | ULTRAPOWER Dual Battery Charger | ker-10685 | 119.95 | 1 | 119.95 | Each | Offshoreelectrics | Battery Charger for EFS Battery Pack | Battery Charger for above Batteries | https://www.offshoreelectrics.com/proddetail.php?prod=ker-10685
5 |  |  |  |  | 0
6 |  |  |  |  | 0
7 |  |  |  |  | 0
8 |  |  |  |  | 0
9 |  |  |  |  | 0
10 |  |  |  |  | 0
 |  |  | Order Total |  | 833.76
*items to remember:
please give us time to purchase - same day requests may not be possible to fulfill
please consider shipping time - same day receipt of item is not possible and rush shipping (overnight or 2-day) should be avoided (as stewards of federal funds, we need to spend them as frugally and responsibly as possible)
if possible, please lump orders from the same vendor together (this will save on shipping and workload)
if possible, please keep overall orders to 10 items or less
If you receive quotes, please send to mcecsdra@pdx.edu for review - shipping address on quotes should be as follows: |  |  |  |  |  |  | SHIP-TO: Helen Frey Portland State University College of Engineering 1930 SW 4th Avenue, Ste 500L Portland, OR 97201 c 503 703 1157 frey@pdx.edu

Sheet: Date 2-28-2019
UTEAP DRA Purchasing Spreadsheet (TEMPLATE)
* COPY this template into your own UTEAP folder, fill out (new sheet for each purchase request), and send to PI with mcecsdra@pdx.edu Cc'ed
How the parts listed below will be used for the project (one sentence): |  |  |  |  |  | These items will help us continue design work on the pump for the Electric Feed System
Item | Part Name | Part Number | Unit Price | Quantity | Total Price | Unit of item (e.g. each pack, case, etc.) | Vendor | Description of Item | Notes (comments, weblink to item, etc.)
1 | Tapered Roller Bearing | 5709K42 | 38.64 | 2 | 77.28 | Each | McMaster | IPA pump bearings | Bearings required for the Electric Feed System | https://www.mcmaster.com/5709k42
2 | 1/2" Flowserve shaft seal | 5NC02 | 18.49 | 3 | 55.47 | Each | Grainger | IPA pump seals | Seals required for the Electric Feed System | https://www.grainger.com/product/FLOWSERVE-1-2-Replacement-Pump-Shaft-5NC02
3 | HATCHBOX 3D PLA-1KG3.00-BLK PLA 3D Printer Filament, Dimensional Accuracy +/- 0.03 mm, 1 kg Spool, 3.00 mm, Black | 3D PLA-1KG3.00-SLV | 22.99 | 1 | 22.99 | Spool | By HATCHBOX on Amazon.com | 3D Printer Filament | 3D Printer inputs required for fabrication | https://www.amazon.com/dp/B019EFB79E/ref=twister_B01FKESAMA?_encoding=UTF8&th=1
4 |  |  |  |  | 0
 |  |  | Order Total |  | 155.74
*items to remember:
please give us time to purchase - same day requests may not be possible to fulfill
please consider shipping time - same day receipt of item is not possible and rush shipping (overnight or 2-day) should be avoided (as stewards of federal funds, we need to spend them as frugally and responsibly as possible)
if possible, please lump orders from the same vendor together (this will save on shipping and workload)
if possible, please keep overall orders to 10 items or less
If you receive quotes, please send to mcecsdra@pdx.edu for review - shipping address on quotes should be as follows: |  |  |  |  |  |  | SHIP-TO: Helen Frey Portland State University College of Engineering 1930 SW 4th Avenue, Ste 500L Portland, OR 97201 c 503 703 1157 frey@pdx.edu

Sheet: Date 3-04-2019
UTEAP DRA Purchasing Spreadsheet (TEMPLATE)
* COPY this template into your own UTEAP folder, fill out (new sheet for each purchase request), and send to PI with mcecsdra@pdx.edu Cc'ed
How the parts listed below will be used for the project (one sentence): |  |  |  |  |  | These items will help us continue design work on the pump for the Electric Feed System
Item | Part Name | Part Number | Unit Price | Quantity | Total Price | Unit of item (e.g. each pack, case, etc.) | Vendor | Description of Item | Notes (comments, weblink to item, etc.)
1 | Kennametal - DNMG332 MP Grade KC5010 Carbide Turning Insert | 6463731 | 24.00 | 1 | 24.00 | Each | MSC Direct | CNC Turning Insert | Used in machining heat-resistant/tough-to-machine materials | https://www.mscdirect.com/product/details/06463731
2 | Kennametal - DNMG331 FF Grade KC5010 Carbide Turning Insert | 2292282 | 24.00 | 1 | 24.00 | Each | MSC Direct | CNC Turning Insert | Used in machining heat-resistant/tough-to-machine materials | https://www.mscdirect.com/product/details/02292282
 |  |  | Order Total |  | 48.00
*items to remember:
please give us time to purchase - same day requests may not be possible to fulfill
please consider shipping time - same day receipt of item is not possible and rush shipping (overnight or 2-day) should be avoided (as stewards of federal funds, we need to spend them as frugally and responsibly as possible)
if possible, please lump orders from the same vendor together (this will save on shipping and workload)
if possible, please keep overall orders to 10 items or less
If you receive quotes, please send to mcecsdra@pdx.edu for review - shipping address on quotes should be as follows: |  |  |  |  |  |  | SHIP-TO: Helen Frey Portland State University College of Engineering 1930 SW 4th Avenue, Ste 500L Portland, OR 97201 c 503 703 1157 frey@pdx.edu

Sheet: Date 4-3-2019
UTEAP DRA Purchasing Spreadsheet (TEMPLATE)
* COPY this template into your own UTEAP folder, fill out (new sheet for each purchase request), and send to PI with mcecsdra@pdx.edu Cc'ed
How the parts listed below will be used for the project (one sentence): |  |  |  |  |  | These items will help us continue design work on the pump for the Electric Feed System
Item | Part Name | Part Number | Unit Price | Quantity | Total Price | Unit of item (e.g. each pack, case, etc.) | Vendor | Description of Item | Notes (comments, weblink to item, etc.)
1 | Aluminum bar stock 6061 | 8975K631 | 75.61 | 1 | 75.61 | Each | McMaster | Aluminum bar: 5" wide, 2" thick, 1 foot long | Aluminum bar used for fabrication of test structure | https://www.mcmaster.com/8975k631
2 | Aluminum bar stock 6061 | 9418T159 | 134.74 | 1 | 134.74 | Each | McMaster | Aluminum bar: 5" wide, 3" thick, 1 foot long | Aluminum bar used for fabrication of test structure | https://www.mcmaster.com/9418T159
 |  |  | Order Total |  | 210.35
*items to remember:
please give us time to purchase - same day requests may not be possible to fulfill
please consider shipping time - same day receipt of item is not possible and rush shipping (overnight or 2-day) should be avoided (as stewards of federal funds, we need to spend them as frugally and responsibly as possible)
if possible, please lump orders from the same vendor together (this will save on shipping and workload)
if possible, please keep overall orders to 10 items or less
If you receive quotes, please send to mcecsdra@pdx.edu for review - shipping address on quotes should be as follows: |  |  |  |  |  |  | SHIP-TO: Helen Frey Portland State University College of Engineering 1930 SW 4th Avenue, Ste 500L Portland, OR 97201 c 503 703 1157 frey@pdx.edu

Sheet: END mills order
CALL OR EMAIL DARREN FROM MESHER TOOLS Sam A. Mesher Tool Company 1704 NW Johnson St Portland OR 97209 (503) 227-6609 Fax (503) 227-7159 meshertool@gmail.com

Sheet: Date 4-21-2019
UTEAP DRA Purchasing Spreadsheet (TEMPLATE)
* COPY this template into your own UTEAP folder, fill out (new sheet for each purchase request), and send to PI with mcecsdra@pdx.edu Cc'ed
How the parts listed below will be used for the project (one sentence): |  |  |  |  |  | These items will help us continue design work on the pump for the Electric Feed System
Item | Part Name | Part Number | Unit Price | Quantity | Total Price | Unit of item (e.g. each pack, case, etc.) | Vendor | Description of Item | Notes (comments, weblink to item, etc.)
1 | 4-40 Socket Head Screws | 90128A113 | 4.55 | 1 | 4.55 | Each | McMaster | Zinc-Plated Alloy Steel Socket Head Screw, 4-40 Thread Size, 3/4" Long | Head Screw for the Electric Feed System | https://www.mcmaster.com/standard-socket-head-screws
 |  |  | Order Total |  | 4.55
*items to remember:
please give us time to purchase - same day requests may not be possible to fulfill
please consider shipping time - same day receipt of item is not possible and rush shipping (overnight or 2-day) should be avoided (as stewards of federal funds, we need to spend them as frugally and responsibly as possible)
if possible, please lump orders from the same vendor together (this will save on shipping and workload)
if possible, please keep overall orders to 10 items or less
If you receive quotes, please send to mcecsdra@pdx.edu for review - shipping address on quotes should be as follows: |  |  |  |  |  |  | SHIP-TO: Helen Frey Portland State University College of Engineering 1930 SW 4th Avenue, Ste 500L Portland, OR 97201 c 503 703 1157 frey@pdx.edu

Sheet: Date 4-23-2019
UTEAP DRA Purchasing Spreadsheet (TEMPLATE)
* COPY this template into your own UTEAP folder, fill out (new sheet for each purchase request), and send to PI with mcecsdra@pdx.edu Cc'ed
How the parts listed below will be used for the project (one sentence): |  |  |  |  |  | These items will help us continue design work on the pump for the Electric Feed System
Item | Part Name | Part Number | Unit Price | Quantity | Total Price | Unit of item (e.g. each pack, case, etc.) | Vendor | Description of Item | Notes (comments, weblink to item, etc.)
1 | Black-Oxide Alloy Steel Socket Head Screw | 91251A540 | 7.86 | 1 | 7.86 | Each | McMaster | 1/4"-20 Thread Size, 3/4" Long | Screws used for the EFS | https://www.mcmaster.com/91251a540
2 | Alloy Steel Shoulder Screw | 91259A101 | 3.91 | 16 | 62.56 | Each | McMaster | 1/4" Shoulder Diameter, 3-1/4" Shoulder Length, 10-24 Thread | Screws used for the EFS | https://www.mcmaster.com/91259a101
 |  |  | Order Total |  | 70.42
*items to remember:
please give us time to purchase - same day requests may not be possible to fulfill
please consider shipping time - same day receipt of item is not possible and rush shipping (overnight or 2-day) should be avoided (as stewards of federal funds, we need to spend them as frugally and responsibly as possible)
if possible, please lump orders from the same vendor together (this will save on shipping and workload)
if possible, please keep overall orders to 10 items or less
If you receive quotes, please send to mcecsdra@pdx.edu for review - shipping address on quotes should be as follows: |  |  |  |  |  |  | SHIP-TO: Helen Frey Portland State University College of Engineering 1930 SW 4th Avenue, Ste 500L Portland, OR 97201 c 503 703 1157 frey@pdx.edu
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

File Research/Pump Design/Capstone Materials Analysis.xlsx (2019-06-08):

Material | Density (g/cc) | Young's Modulus (GPa) | Yield Strength (MPa) | Poissons Ratio | Shear Modulus (GPa) | Machinability Est. (%) | Ductility (Cryogenic) | Link to data source
Al 6061-T6 | 2.7 | 68.9 | 276 | 0.33 |  | 50 |  | http://matweb.com/search/datasheet.aspx?MatGUID=b8d536e0b9b54bd7b69e4124d8f1d20a
Stainless 304 | 8 | 193 | 215 | 0.29 | 77 | 44 |  | http://matweb.com/search/DataSheet.aspx?MatGUID=abc4415b0f8b490387e3c922237098da&ckck=1
Stainless 304L | 8 | 193 - 200 | 210 |  |  |  |  | http://matweb.com/search/DataSheet.aspx?MatGUID=e2147b8f727343b0b0d51efe02a6127e
Stainless 316 (annealed bar) | 8 | 193 | 240 |  |  | Find its somewhat a little bit hard to machine |  | http://www.pennstainless.com/stainless-grades/300-series-stainless-steel/316l-stainless-steel/
Stainless 303 | 8.027 | 193 | 415 | 0.25 | 77.2 |  |  | http://www.pennstainless.com/stainless-grades/300-series-stainless-steel/303-stainless-steel/
Stainless 321/321H | 7.92 | 193 | 205 |  |  |  |  | https://www.sandmeyersteel.com/321-321H.html#MechanicalProperties

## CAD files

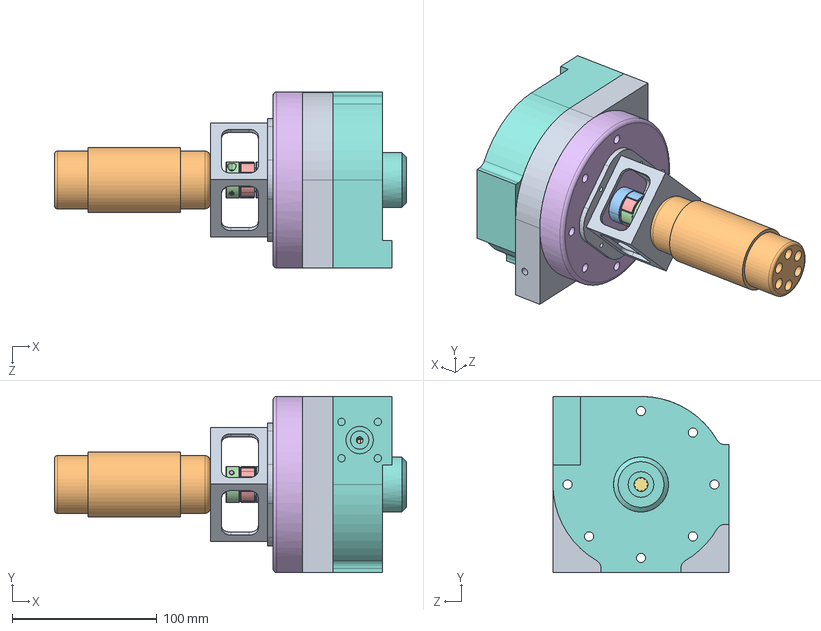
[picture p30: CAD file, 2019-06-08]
2.2kN Design/CAD/LOX_Pump/LOX_Pump_Assembly.SLDASM
243.6 x 121.9 x 121.9 mm
Case_1_CRYO_double_bearing
ceramic_bearing
Shaft Collar_double_bearing
Thrust_Bearing
Bearing Compression plate
Bearing_Plate_CRYO
Impeller_CRYO
Case_2_CRYO
Square Direct Motor Mount
Motor
Coupler_A.STEP
Coupler_B.STEP
Dampener.STEP
M3x12_Screw.STEP x 2

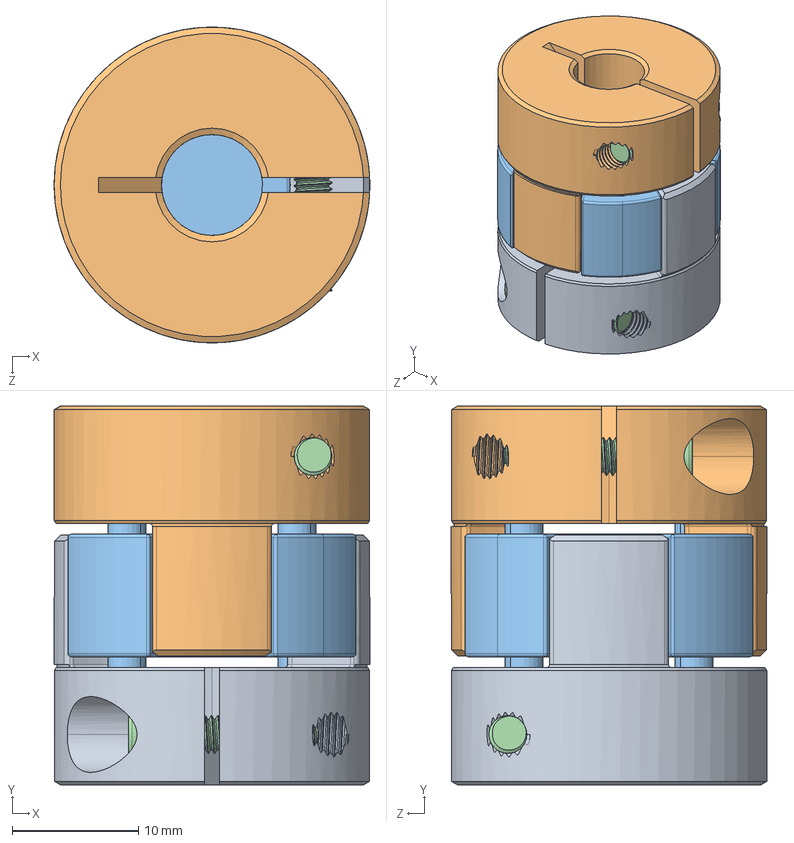
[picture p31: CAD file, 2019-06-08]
2.2kN Design/CAD/IPA_Pump/Coupler_8mm_to_8mm.SLDASM
25.0 x 30.0 x 25.0 mm
Coupler_A.STEP
Coupler_B.STEP
Dampener.STEP
M3x12_Screw.STEP x 2

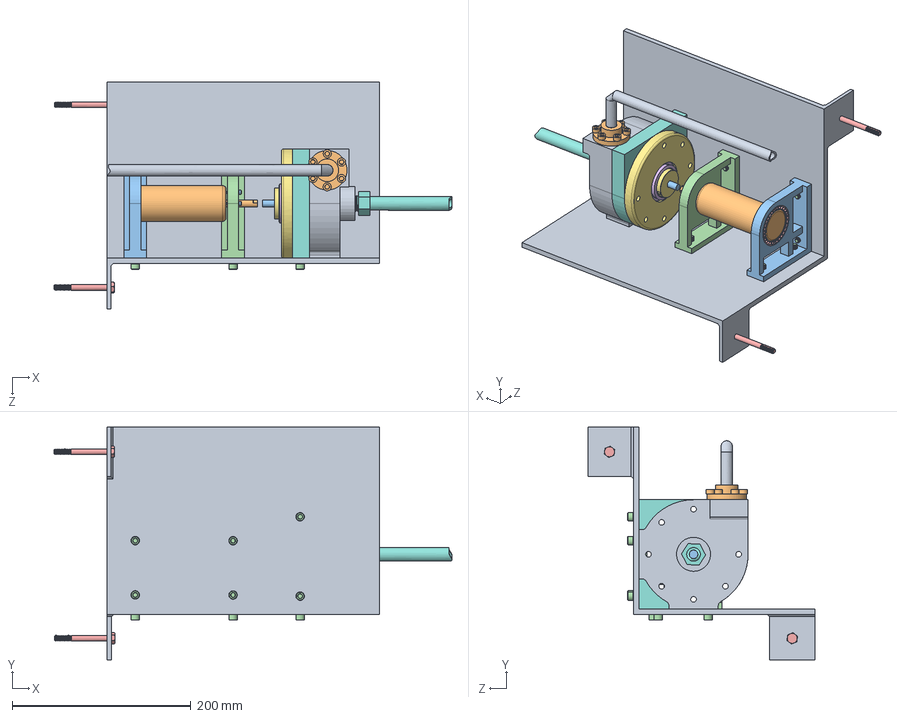
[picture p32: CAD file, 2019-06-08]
2.2kN Design/CAD/IPA_Pump/EFS_IPA_Pump_Iteration2.SLDASM
444.8 x 260.4 x 254.0 mm
Baseplate
Motor
Motor_Support_Rear
Motor_Support_Front
Motor_Vibration_Damper
Diffuser
Bearing_Plate
Case_1_IPA
Case_2_IPA
Diffuser_Flange
Impeller_Shaft_Combined_IPA
Flowserve_Seal
1_inch_collar
Thrust_Bearing
ThrustBearingCollar
Inlet_Plumbing
OutletPlumbing
Flange_Screw x 6
91251A114_BLACK-OXIDE ALLOY STEEL SOCKET HEAD CAP SCREW x 4
92196A540_18-8 STAINLESS STEEL SOCKET HEAD CAP SCREW x 11
STAINLESS STEEL HEX HEAD CAP SCREW x 2

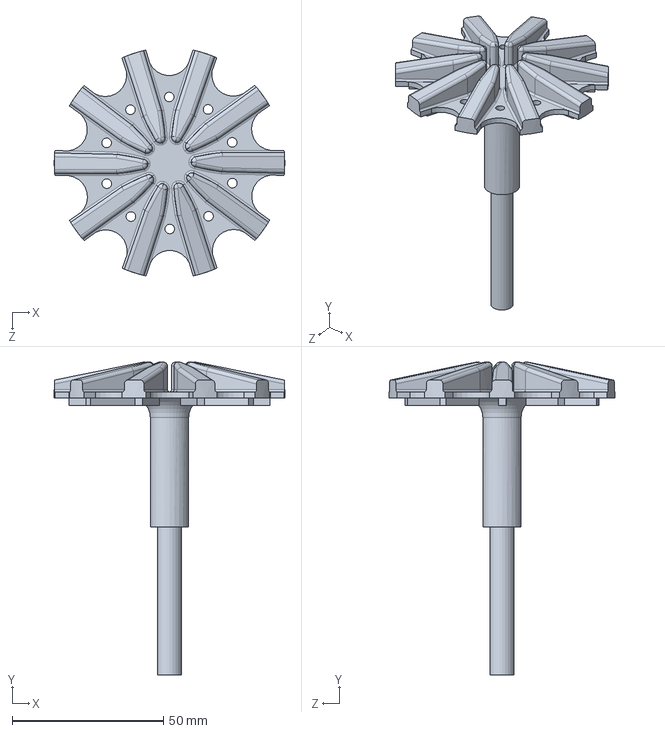
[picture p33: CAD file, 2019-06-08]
2.2kN Design/CAD/Impeller_Concept_Backpressure_Barske.SLDPRT
76.2 x 103.4 x 74.6 mm

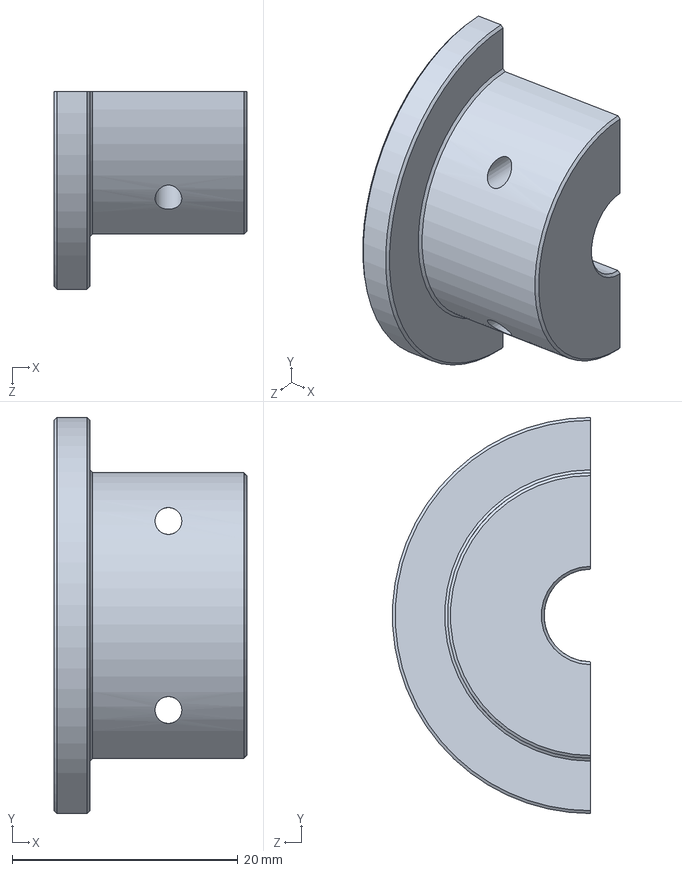
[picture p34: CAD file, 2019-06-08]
2.2kN Design/CAD/IPA_Pump/Collar_Sectional.SLDPRT
17.1 x 35.1 x 17.5 mm

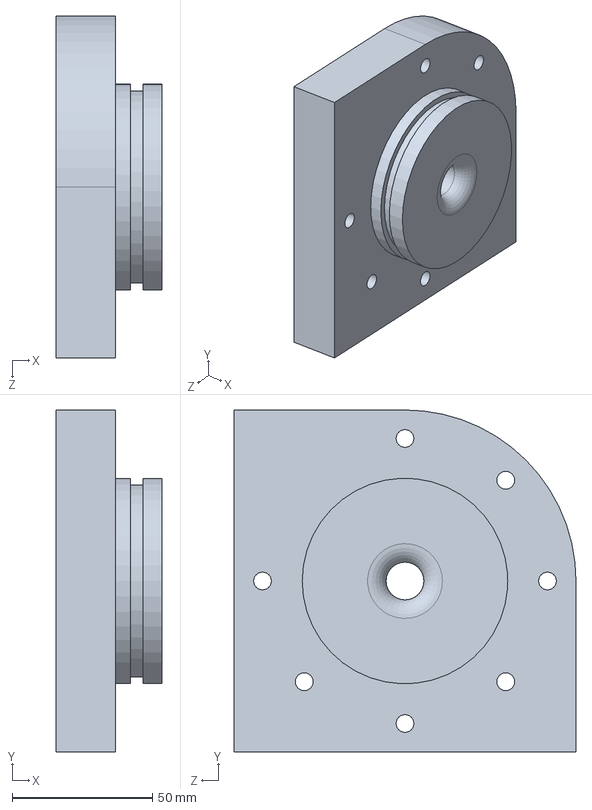
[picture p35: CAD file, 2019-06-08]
2.2kN Design/CAD/LOX_Pump/Case_1_CRYO_double_bearing.SLDPRT
37.9 x 121.9 x 121.9 mm

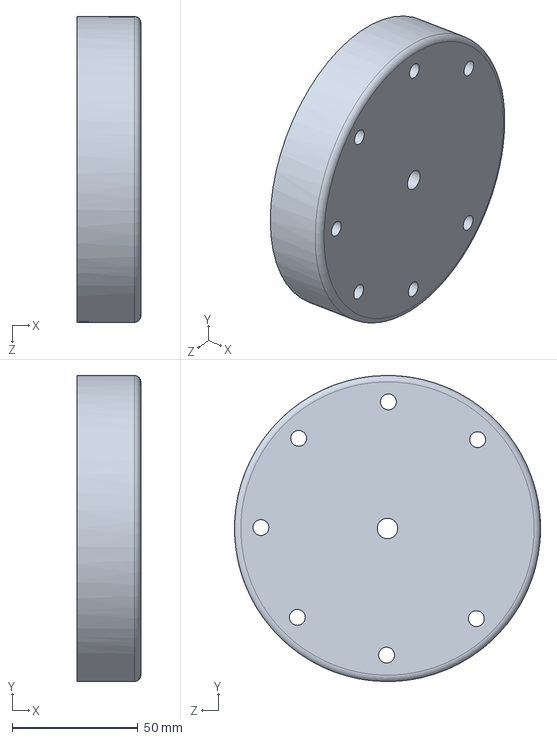
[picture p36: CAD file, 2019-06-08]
2.2kN Design/CAD/IPA_Pump/Bearing_Plate.SLDPRT
25.4 x 121.9 x 121.9 mm

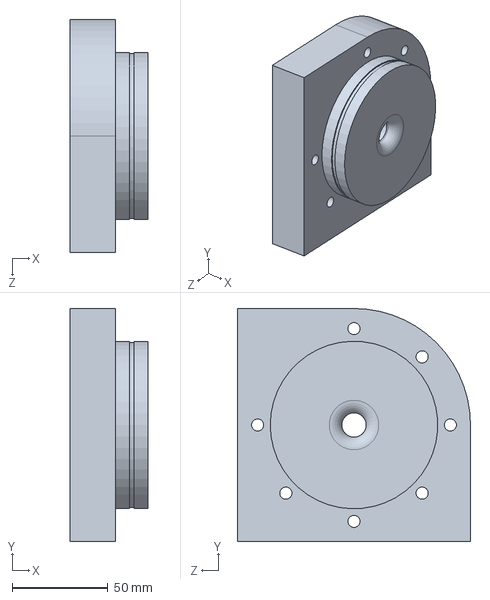
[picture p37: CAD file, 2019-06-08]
2.2kN Design/CAD/IPA_Pump/Case_1_IPA.SLDPRT
40.9 x 121.9 x 121.9 mm

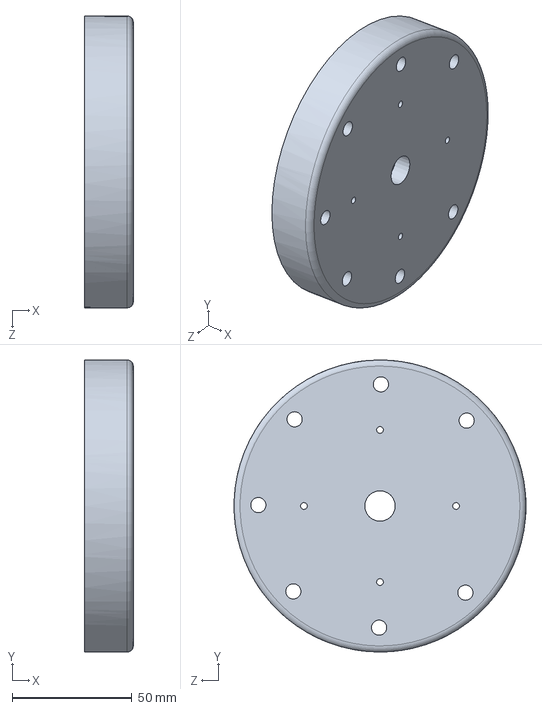
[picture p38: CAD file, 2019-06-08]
2.2kN Design/CAD/LOX_Pump/Bearing_Plate_CRYO.SLDPRT
20.3 x 121.9 x 121.9 mm

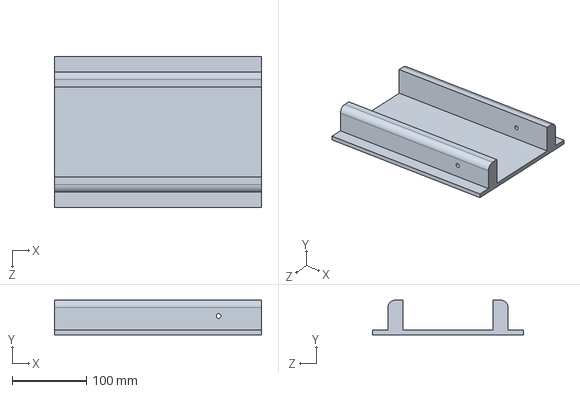
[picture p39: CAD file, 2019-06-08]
2.2kN Design/CAD/IPA_Pump/Baseplate.SLDPRT
279.4 x 47.0 x 203.2 mm

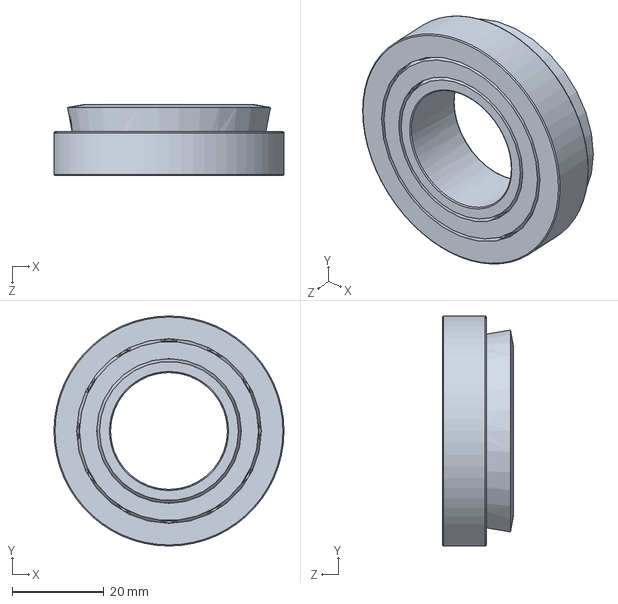
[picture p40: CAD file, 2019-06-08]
2.2kN Design/CAD/LOX_Pump/Thrust_Bearing.SLDPRT
50.0 x 50.0 x 15.4 mm

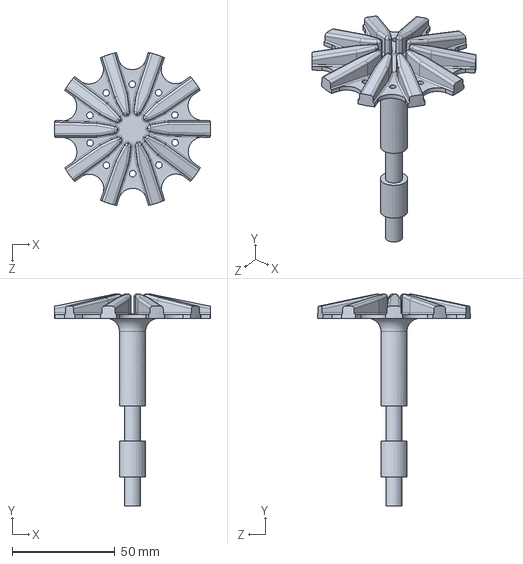
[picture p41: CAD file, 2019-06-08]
2.2kN Design/CAD/IPA_Pump/Impeller_IPA_Extended.SLDPRT
76.2 x 103.4 x 74.6 mm

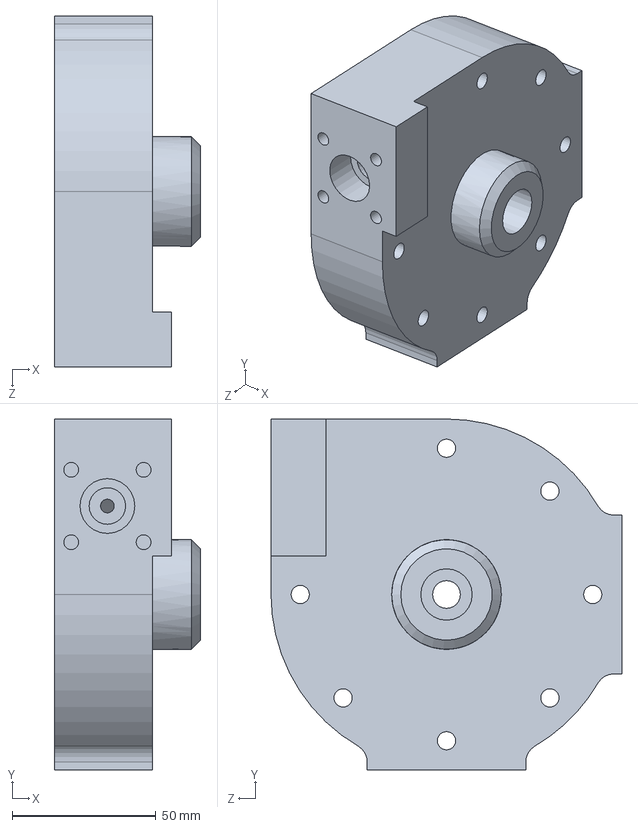
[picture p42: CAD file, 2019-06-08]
2.2kN Design/CAD/LOX_Pump/Case_2_CRYO.SLDPRT
50.8 x 121.9 x 121.9 mm

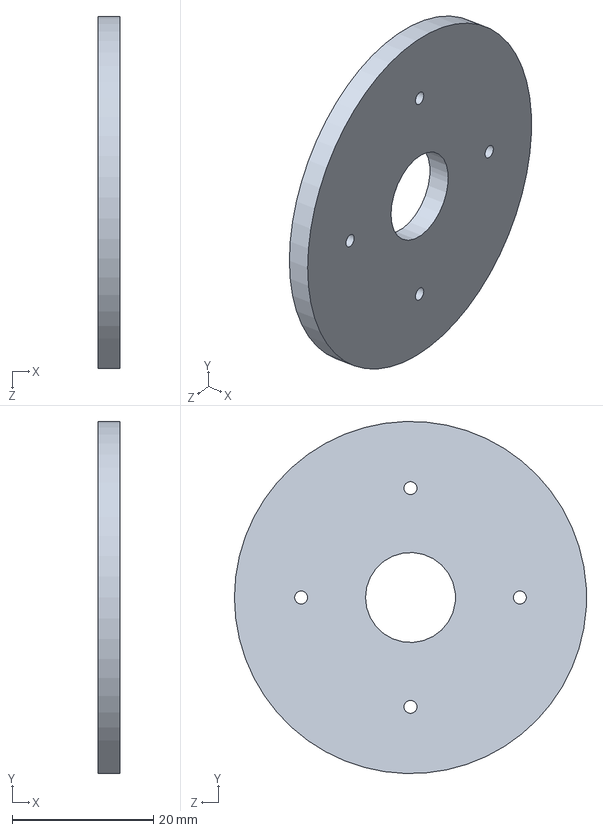
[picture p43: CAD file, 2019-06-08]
2.2kN Design/CAD/IPA_Pump/SealRetainer.SLDPRT
3.17 x 49.8 x 49.8 mm

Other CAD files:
2.2kN Design/CAD/IPA_Pump/Coupler.SLDASM
2.2kN Design/CAD/IPA_Pump/L30xD25 CouplerASM 8to8.SLDASM
2.2kN Design/CAD/LOX_Pump/Impeller_CRYO.SLDPRT
2.2kN Design/CAD/LOX_Pump/Square Direct Motor Mount.SLDPRT
2.2kN Design/Analysis/CFD/It2_Impeller_Shaft_Combined_NoFillets.x_t
2.2kN Design/CAD/IPA_Pump/1_inch_collar.SLDPRT
2.2kN Design/CAD/IPA_Pump/90298A550_18-8 STAINLESS STEEL SHOULDER SCREW.SLDPRT
2.2kN Design/CAD/IPA_Pump/91251A114_BLACK-OXIDE ALLOY STEEL SOCKET HEAD CAP SCREW.SLDPRT
2.2kN Design/CAD/IPA_Pump/91259A101_ALLOY STEEL SHOULDER SCREW.SLDPRT
2.2kN Design/CAD/IPA_Pump/92196A540_18-8 STAINLESS STEEL SOCKET HEAD CAP SCREW.SLDPRT
2.2kN Design/CAD/IPA_Pump/95462A029_GRADE 5 STEEL HEX NUT.SLDPRT
2.2kN Design/CAD/IPA_Pump/Bearing Collar as of 4-11-19.SLDPRT
2.2kN Design/CAD/IPA_Pump/Case_1_IPA_Modified.SLDPRT
2.2kN Design/CAD/IPA_Pump/Case_2_IPA.SLDPRT
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

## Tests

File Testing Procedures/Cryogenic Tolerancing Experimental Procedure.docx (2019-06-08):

Test Description:

Use 10lbs (~1.5 gallons) of liquid nitrogen (LN2) to run a series of individual pump component cooling tests to identify the geometric contraction under cryogenic conditions.

- Initial Room Temperature = 22°C
- Liquid Cryogen Temperature = -196°C
- Component Submersion Time = 120 seconds

These tests will attempt to simulate operating conditions for the pump components to finalize the cryo pump design geometry. Results will be extrapolating to future use with liquid oxygen which boils at -182.19°C

Goals:

- Identify contraction metrics under cryogenic conditions
  - Bore size reduction
  - Impeller shaft diameter reduction
  - Entry and Exit Fitting seal
  - Case bolt tension

Personal protective equipment (PPE)

- Safety Glasses
- Leather Gloves for handling LN2
- Long Sleeves
- Various pliers for part handling and submersion
  - Needle Nose
  - Vise Grips
- Steel wire for component wrapping
- Plywood board Safety Zone for component warm up

Procedure:

Preliminary Measurements

1. Fill out all component measurement sheets for room temp *at end of this document
  a. Impeller
  b. Shaft Collar
  c. Case 1
  d. Seal Retaining Ring
  e. Case 2
  f. Bearing Plate
2. Wrap individual components with steel wire for safe submersion

Liquid Cryogen

3. Acquire 10lbs of LN2 from the SRTC second floor stock room.
  a. Faculty Advisor = Mark Weislogel
  b. Grant Index Number = 244812
  c. Use PSAS dewar if top can be removed,
  d. Acquire open top dewar from SRTC if needed
4. Complete SRTC safety protocol * required only for members acquiring LN2
5. Safely transport LN2 to area outside MME Machine Shop for testing

Test Trials

6. *Using PPE Open LN2 dewar to expose boiling liquid cryogen
7. Submerge component into LN2 for a 120 Seconds

Order of Component Submersion

  a. Impeller
  b. Shaft Coupler
  c. Case 1
  d. Seal Retaining Ring
  e. Case 2
  f. Bearing Plate
8. Carefully measure critical dimensions for submerged component
9. Place cooled component in safe zone to keep from accidental contact
10. Repeat steps 7 - 9 until all components have been submerged and measured
11. *Using PPE Close LN2 dewar lid

Clean Up

12. Safely dispose of remaining LN2
13. Transport cooled components on safety board for long term warm up

Test Day Notes

Measurement Sheet

Impeller

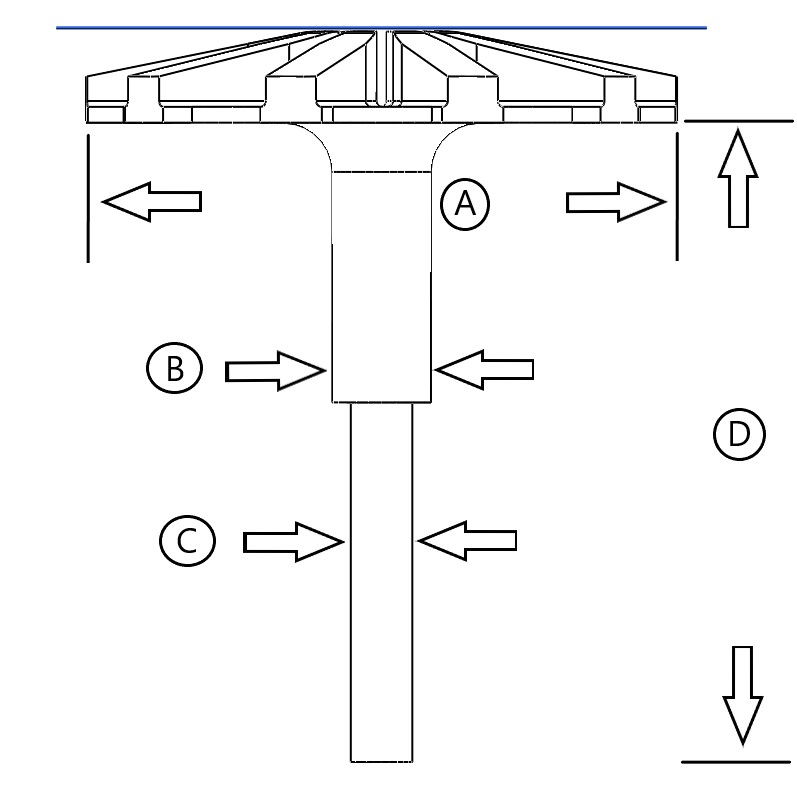
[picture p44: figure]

Component Measured | Room Temp | Cooled | Unit
B: Impeller Shaft (thick) | 0.5001 | 0.4984 | [in]
D: Impeller Shaft Length | 3.247 | 3.240 | [in]

Measurement Sheet

Shaft Collar

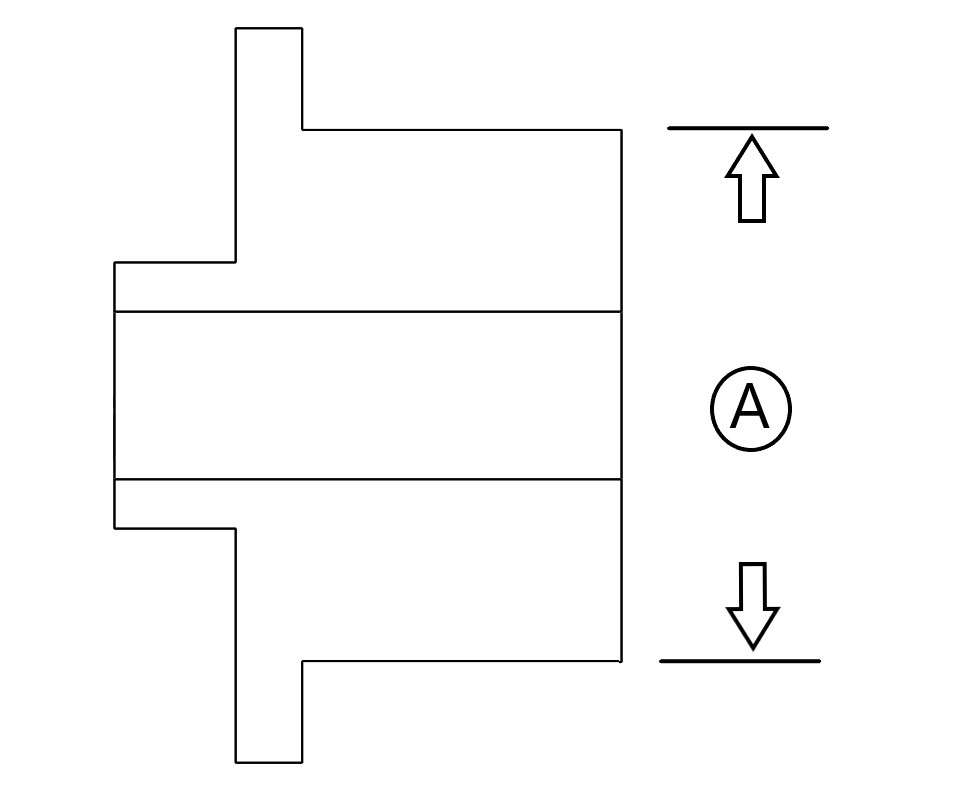
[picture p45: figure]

Component Measured | Room Temp | Cooled | Delta | Unit
A: Bearing Fit Diameter | 0.995 | 0.99197 | 0.00303 | [in]

Measurement Sheet

Case 1

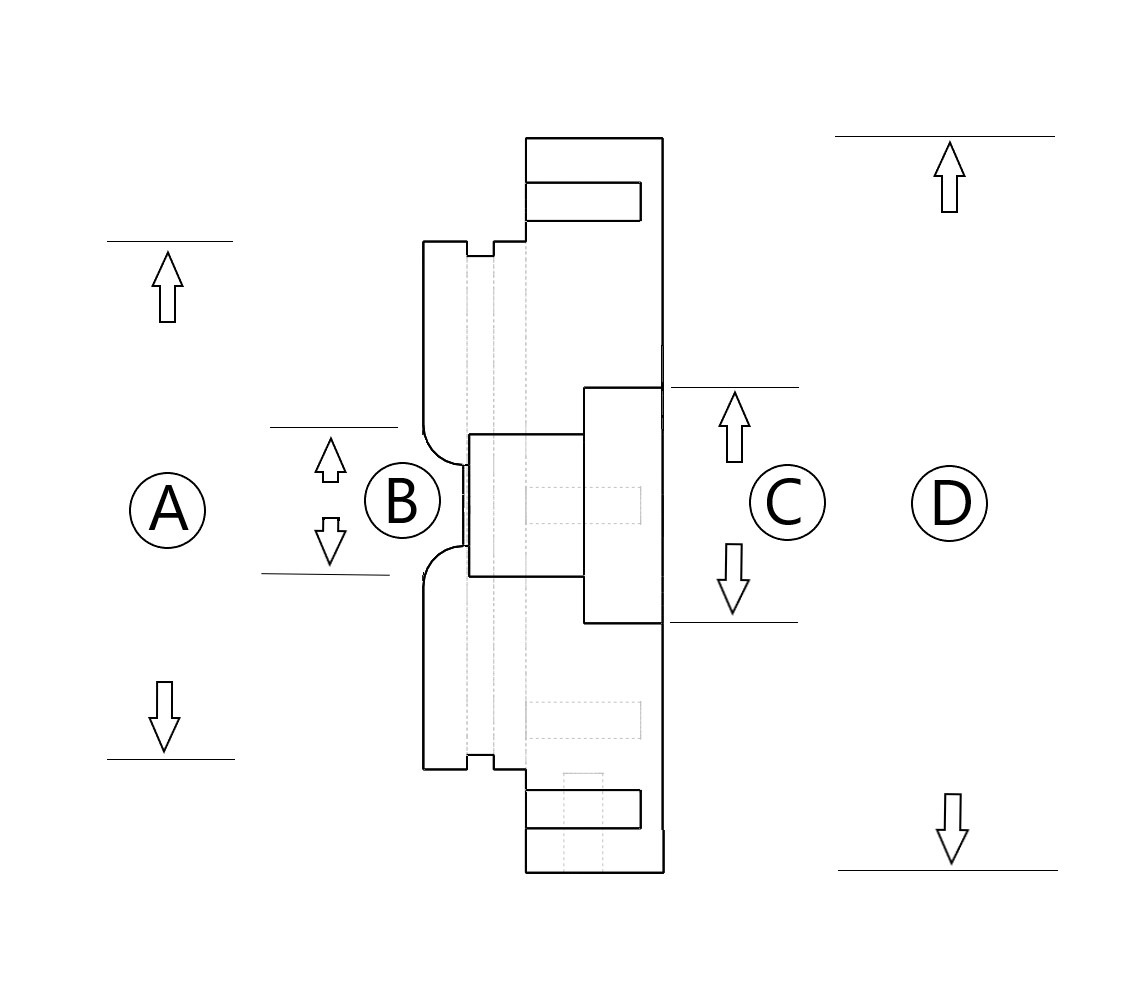
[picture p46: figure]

Component Measured | Room Temp | Cooled | Delta | Unit
A: Impeller Base Extrude Outer Diameter | 3.45013 | 3.440 | 0.01013 | [in]
B: Impeller Entrance Diameter | 0.9308 | 0.9287 | 0.0021 | [in]

Measurement Sheet

Seal Retaining Ring

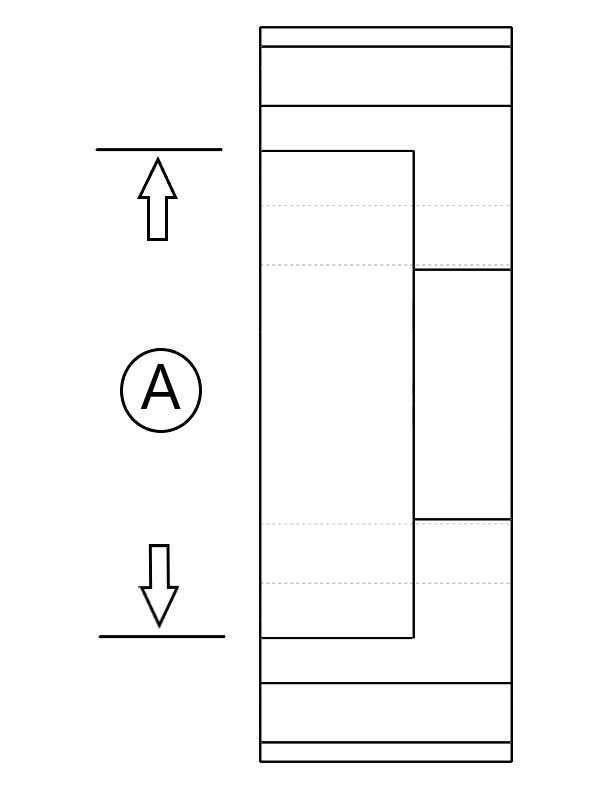
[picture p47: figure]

Component Measured | Room Temp | Cooled | Delta | Unit
A: Seal Insert Diameter | 0.9943 | 0.99187 | 0.00243 | [in]

Measurement Sheet

Case 2

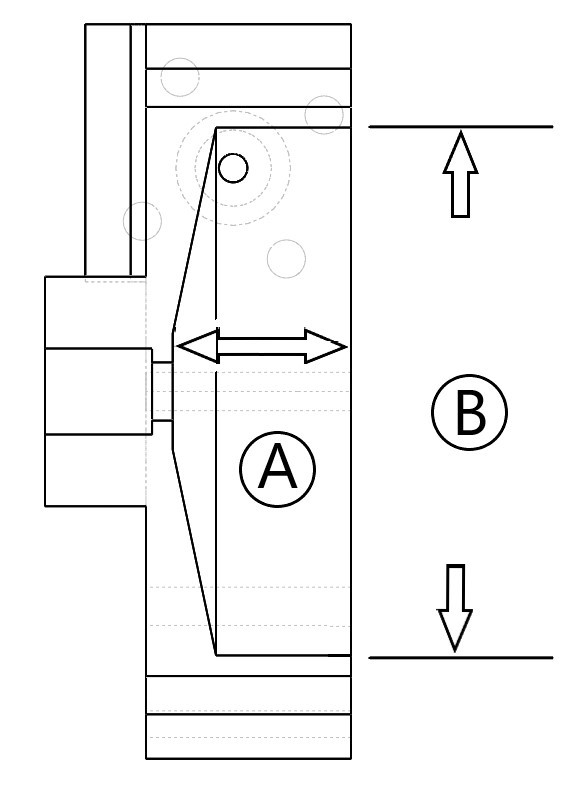
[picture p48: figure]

Component Measured | Room Temp | Cooled | Delta | Unit
A: Impeller Case Depth | 1.167 | 1.159 | 0.008 | [in]
B: Impeller Base Insertion Diameter | 3.4532 | 3.4408 | 0.0124 | [in]

Measurement Sheet

Bearing Plate

Component Measured | Room Temp | Cooled | Delta | Unit
A: Bearing Insert Diameter | 1.9693 | 1.9632 | 0.0061 | [in]

Electric Feed System Test Protocol: Liquid Nitrogen Geometric Contraction

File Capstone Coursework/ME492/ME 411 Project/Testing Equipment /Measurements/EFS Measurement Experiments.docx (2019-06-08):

Things we need to measure:

- Pressure
  - NPSH (in [ft])
  - Chamber
  - Seal
  - Outlet
- Mass flow rate
  - Outlet flow
- Rpm
  - Can also be used to derive kW (along with torque)

Other measurements to consider:

- Torque
- Heat/Temperature

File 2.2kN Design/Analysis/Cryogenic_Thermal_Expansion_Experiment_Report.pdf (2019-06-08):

## Quantifying Thermal Expansion of Aluminum

## Components At Cryogenic Temperatures

Philip Wahl
philwahl@pdx.edu

Portland State Aerospace Society Propulsion: Electric Feed System May 18, 2019

## Introduction

This experiment is designed to identify a quantitative method to design cryogenic components for Portland State Aerospace Society’s Electric Feed System (EFS). The EFS consists of two separate

pumps used to feed isopropyl alcohol (IPA) and liquid oxygen (LOX). Liquid nitrogen (LN2) will

be used in this experiment due to safety requirements. The primary measurements demonstrate

the effects that cryogenic temperatures have on the pump components.

## Theory

Thermal expansion can be theoretically found as[1]:

∆L = Lmα∆T | (1)

Here, ∆L is the dimensional change, Lm is the machined (initial) dimension, α is the coefficient

of thermal expansion, and ∆T is the change in temperature. Note that ∆T = TC − T∞, where TC

is the cooled temperature and T∞ is the ambient temperature of the room. Then the theoretical

cooled length, LC, can be calculated as:

LC = Lm + ∆L | (2)

## Methods

Individual components were submerged in a container of LN2 at TC ≈ −196◦C as shown in Figure

2. 12 distances were measured on the shaft, pump housing components, and bearing collar. The

component measurement points are shown in Appendix A, Figure 4. Measurements were taken 3 to

5 times using micrometers or bore gauges, then averaged to increase accuracy. Each measurement was made initially at an ambient temperature of Tm ≈ 20◦C , then repeated after the component

was submerged for two minutes in the cryogenic fluid. An example of a component before and after

exposure to cryogenic temperatures can be seen in Figure 3.

1

## Results & Conclusion

The experiment showed an average reduction in component size of 0.226%. The measured reduc-

tions in size did not match the theoretical values calculated. However, they displayed a direct linear

correlation to the theoretical results, which can be seen in Figure 1. The relationship between room

temperature, theoretical cooled, and measured cooled dimensions are shown in Table 1.
The trendline polynomial shown in Figure 1 can be substituted into Equation (2) and used to

solve for the target machined dimension to achieve optimal cryogenic performance geometry. This

formula is shown below, and its derivation can be found in Appendix B.

Lo =

(Lc + 0.0014)
(1 + [(1.0028)(α(Tc − T∞))]) | (3)

This formula gives Portland State Aerospace Society a more reliable design criteria for any

propulsion systems that are intended for use with cryogenic fluids, and will be utilized for the

design and tolerancing of the cryogenic electric feed system.

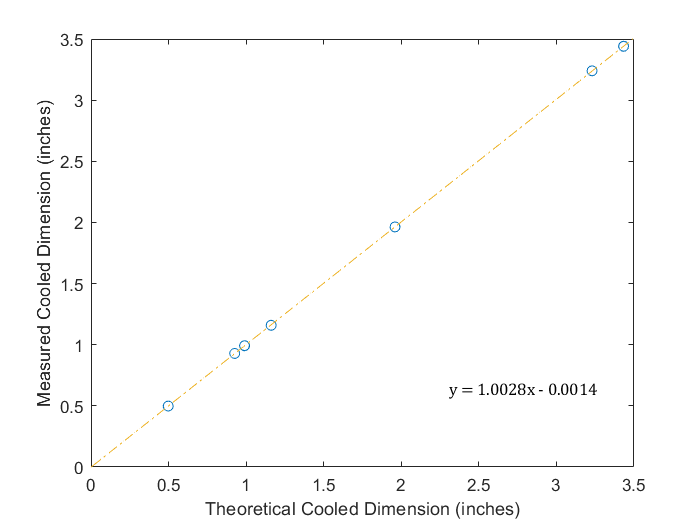
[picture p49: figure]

Figure 1: Measured Component Dimensions vs. Calculated Dimensions

2

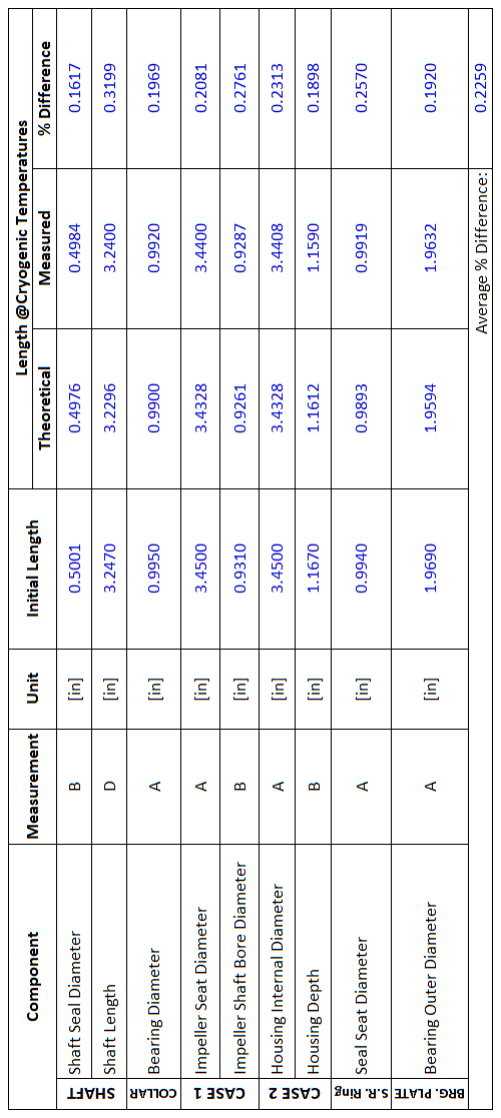
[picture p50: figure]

Table 1: Theoretical & Measured Results of Component Geometries

3

## Appendix A: Additional Figures

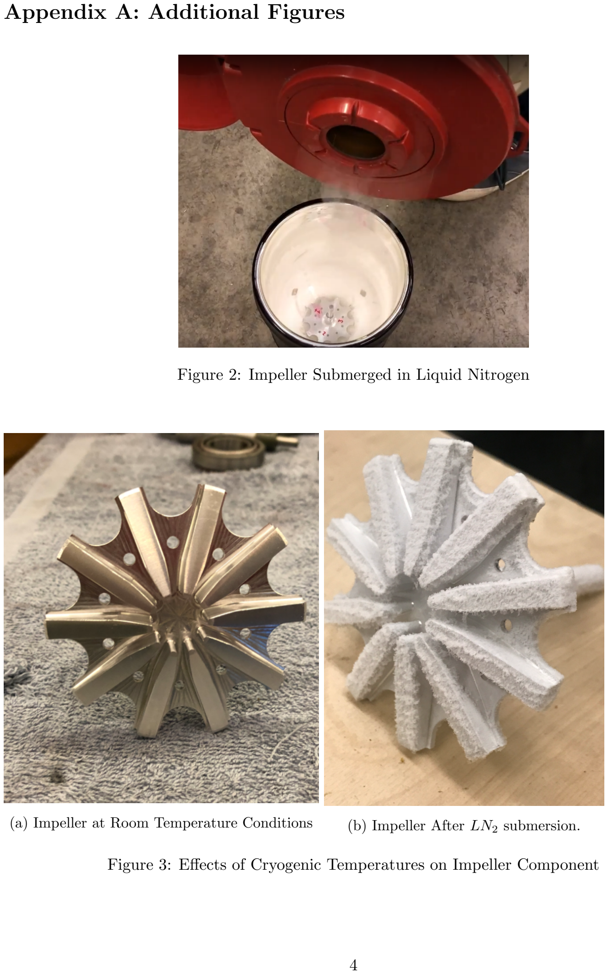
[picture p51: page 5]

Figure 2: Impeller Submerged in Liquid Nitrogen

(a) Impeller at Room Temperature Conditions (b) Impeller After LN2 submersion.

Figure 3: Effects of Cryogenic Temperatures on Impeller Component

4

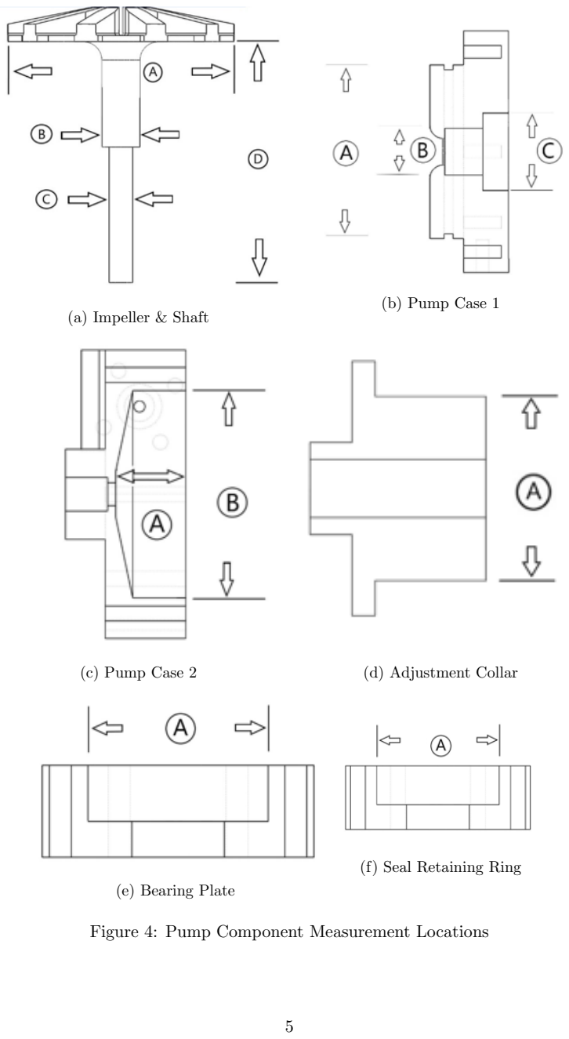
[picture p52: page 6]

(a) Impeller & Shaft
(b) Pump Case 1
(c) Pump Case 2 | (d) Adjustment Collar
(e) Bearing Plate
(f) Seal Retaining Ring

Figure 4: Pump Component Measurement Locations

5

## Appendix B: Sample Calculation

From Equations (1), (2), & Figure 1:

Lc = Lo + ∆L

∆Lactual = m · ∆Ltheoretical + b

= (1.0028)(Loα∆T) + (−0.0014)

⇒ Lc + (0.0014) = Lo(1 + [(1.0028)(α(Tc − T∞))])

Lo =

(Lc + 0.0014)
(1 + [(1.0028)(α(Tc − T∞))])

## Appendix C: References

[1] R. Budynas, K. Nisbett, “Shigley’s Mechanical Engineering Design” (2014, 10thEd.)

6

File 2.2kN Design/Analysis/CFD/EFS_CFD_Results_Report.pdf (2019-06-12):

# Electric Feed System Pump Simulation for

# use in Bi-Propellant Rocket Propulsion

# Systems

### Philip Wahl

### philwahl@pdx.edu

### Portland State University

### ME448 - Computational Fluid Dynamics

### March 22, 2019

## 1 Overview

Portland State Aerospace Society (PSAS) requires the development of an Electric Feed System (EFS) to satisfy the mass flow and pressure requirements of Launch Vehicle 4 (LV4).

LV4 will utilize a bi-propellant propulsion system to generate the required thrust for the rocket to reach the Von K´arm´an Line, or the “Edge of Space”, at approximately 100 km (or 62 mi) altitude. Liquid oxygen (LOX) and isopropyl alcohol (IPA) will be used as

propellants. An EFS is an alternative to traditional pressure tanks or turbopumps used in larger and more expensive rockets. This paper details the computational fluid dynamic (CFD) simulation that has been performed to analyze the chamber pressure of the current

EFS IPA pump design, which is shown in Figure 1. The findings from this analysis will be used to improve the design of the IPA pump. Additionally, they will serve as reference for modeling future LOX simulations.
The primary focus of this simulation is to understand the effects that impeller rotation in the pump case will have on the pressure and velocity distributions of the fluid. The fluid body of the pump will be modeled, starting from a mass flow inlet. The fluid enters this boundary and flows to the pump chamber housing the impeller, with an optimized rotation rate of approximately 36, 000 rpm. The impeller will be treated as a fluid wall rotating within the fluid body. The outlet on the diffuser side of the pump will be treated as a standard pressure outlet. The IPA pump will be modeled with the fluid at room temperature.

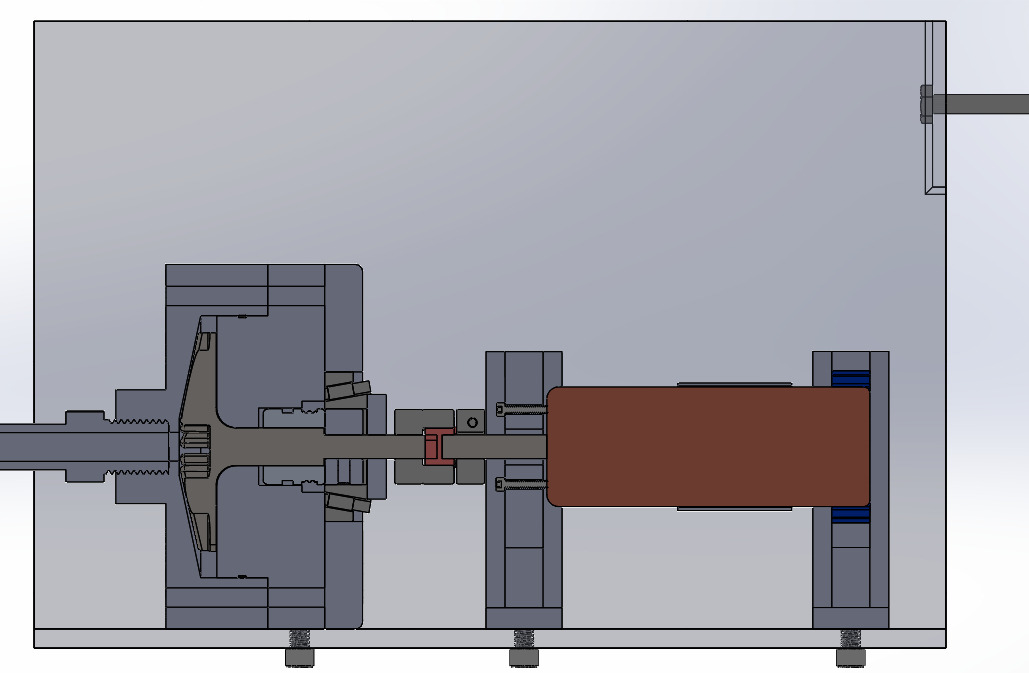
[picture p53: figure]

Figure 1: Cross-Section View of the Current Electric Feed System Design

1

### 1.1 Key Equations

Velocity from Mass Flow Rate[1]:

V =

m˙
ρA | (1)

Reynold’s Number[1]:

Re =

ρV D µ | (2)

Turbulence Intensity[2]:

I = 0.16Re⁻¹/8 | (3)

### 1.2 Nomenclature

- V : Inlet velocity
- m˙ : Mass flow rate
- ρ: Fluid density
- A: Inlet area
- D: Inlet diameter
- µ: Dynamic viscosity
- I: Turbulence intensity
- Re: Reynold’s Number
- ut
: Impeller tip speed

2

## 2 Physical Model and Boundary Conditions:

The fluid continua for this simulation used a constant density, coupled flow model with K − epsilon turbulence. Implicit integration and 2nd-order discretization were used. The inlet boundary was treated as a mass flow inlet with a fixed flow rate of ˙m = 0.33 kg/s.

Implicit unsteady flow physics was used, as steady flow resulted in residuals that would not converge.
The fluid body was treated as a stationary wall. The impeller wall was designated as a rotating reference frame within the fluid body, with a rotation motion of 35718 rpm rotating around the wall. A blended wall function with E = 9.0, κ = 0.42 was used. The impeller and fluid boundaries are shown in Figure 2b. The outlet boundary was set as a standard outlet. The flow pattern is visualized in Figure 2a. The inlet parameters are shown in Appendix A, Table 1.


(a) Pump Flow Pattern Boundaries
(b) Fluid Body With Impeller Walls Shown

Figure 2: Flow Boundaries

3

## 3 CFD Software Features

This simulation was considered a high turbulence case, with a turbulence intensity of I = 0.046 (found using Equation 3). This aligned with intuition, noting a high Reynold’s number at Re = 21711. K − Epsilon was selected as the turbulence model, as it provided the most

optimal residuals within a reasonable number of iterations.

## 4 CFD Mesh

A polyhedral mesh was used with “Surface Remesher” enabled. The initial mesh used was 0.5 in, a course mesh relative to the size of the system being modeled. This mesh size converged for the first 80 iterations, but diverged sharply after this point, as shown in Figure
6. The mesh was then continually refined until an optimal base size of 0.2 in was determined. This base size resulted in acceptable convergence, with all residuals dropping below 0.001 while exhibiting reasonable computation times. The model converged in approximately 500 iterations. The course and fine mesh can be seen in Figure 3a and Figure 3b, respectively.


(a) Course Mesh (0.5 in)


(b) Fine Mesh (0.2 in)

Figure 3: Mesh Scenes

4

## 5 Results and Discussion

The velocity vector scene of the pump at approximately 36000 rpm can be seen in Figure
5. The calculated impeller tip speed for the pump is 254 m
s

. It can be seen that while the velocities at the impeller’s edge are similar in magnitude to this target value, the precise velocity is not reached. This points to potential faults in the model’s reference frame setup. Additionally, while rotational energy is being transferred to the pump chamber, it does not appear to be transferring proportionally to the flow outlet.
The pressure scalar cross-section shown in Figure 4 further illustrates this discrepancy. While the pump chamber in the model reaches the desired pressure range of 300-450 psi, the pressure leaving the pump at the diffuser is approximately 30% lower than inside the

chamber. This could be caused either by the physics of the model, the boundary conditions selected, or the pump geometry itself. The residuals for this simulation can be seen in Figure 7.
Modeling the flow with a stagnation pressure inlet and pressure outlet provided the results shown Appendix A, Figure 9. While the pressure distribution in the chamber shows an appropriate gradient from the impeller eye out to the chamber wall, the pressure leaving the diffuser is also substantially lower than desired. Velocity inlet with mass flow out is also shown in Appendix B, Figure 8. This model resulted in appropriate pressure release into the diffuser, but gives an inlet pressure of approximately 225 psi, five times greater than the target inlet pressure of 45 psi.

5


Figure 4: Pressure Distribution Cross-Section of Pump Chamber at

≈ 36000 rpm

Figure 5: Velocity Profile of Pump Chamber at

≈ 36000 rpm

6


Figure 6: Divergent Residuals for Course Mesh (0.5 in Base Size) Figure 7: Converged Residuals for Fine Mesh (0.2 in Base Size)

7

## 6 Conclusion

While the results from this simulation have not provided an accurate model of the theoretical pump design, it points toward several areas of improvement, both for CFD modeling of the pump and the design itself. The primary area of concern with the simulation’s results is the drop in pressure from the pump chamber to the outlet. Multiple boundary condition configurations were tested, including mass flow inlet with pressure outlet, stagnation inlet with mass flow outlet, stagnation inlet with pressure outlet, and velocity inlet with pressure outlet. The pressure distributions of alternative boundary condition configurations can be seen in Appendix B, Figure 8 and Figure 9. Moving forward, the boundary conditions of this model will continue to be reconfigured to achieve the optimal pressure results.
The fluid physics continua could also be a cause of the discrepancies in the results. A possible alternative is to reconstruct the model to simulate the rotation of the impeller as a solid rather than a fluid wall. It is possible the the transfer of energy in the simulation is not properly represented without the inertia of the solid body accounted for.
Finally, the results could point toward the need to improve the pump design itself. Moving forward, CFD models with alternative outlet diameters will continue to be tested to see if the pump’s design can be optimized to further resist flow in the system. Additionally, the pump volute design can potentially be improved to optimize the flow pattern for greater pressure gain. Currently, the pump chamber is concentric about the impeller. However, traditional pump volutes feature a unique flow path that diverges at the outlet to convert kinetic energy from velocity to pressure[1]. This configuration will be modeled in the future to compare to

the final results that are found for the concentric chamber.

8

## Appendices

### Appendix A: Tables

Table 1: Inlet Flow Properties of IPA[1]

Property | Symbol | Units | Value
Area | A | [mm²
| | ] | 81.07
Mass Flow | ˙m | [ lg s
| | ] | 0.33
Velocity | V | [ m s
| | ] | 5.17
Pressure | P | [psi] | 45
Temperature | T | [
| | ◦C] | 20
Dynamic Viscocity | µ | [P a · s] 0.0019
Density | ρ | [ kg m³
| | ] | 786
Reynold’s Number | Re | [-] | 21711
Turbulence Intensity | I | [-] | 0.046

### Appendix B: Additional Figures


Figure 8: Pressure Distribution With Velocity In, Mass Flow Out BCs

9


Figure 9: Pressure Distribution With Pressure In, Pressure Out BCs

### Appendix C: References

[1] T. Bergman & F. Incropera (2011),“Fundamentals of Heat and Mass Transfer” (7thEd).
[2] ANSYS, Inc. (2018), “ANSYS Fluent User’s Guide, Release 19.0”, Equation (6.68).

10

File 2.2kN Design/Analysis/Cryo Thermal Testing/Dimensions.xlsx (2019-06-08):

 | Impeller | Average
 | A | 2.9818 | 2.9818 | 2.9816 | 2.9819 | 2.9819 | 2.9818
 | B | 0.5001 | 0.5 | 0.5 | 0.5001 | 0.5003
 | C | 0.3139666667 | 0.3146 | 0.314 | 0.3125 | 0.3136 | 0.3148 | 0.3143
 | D | 3.245863636 | 3.243 | 3.26 | 3.245 | 3.236 | 3.2325 | 3.239 | 3.2495 | 3.259 | 3.2475 | 3.251 | 3.242
 | Bearing Collar
OD | A | 0.995 | 0.995
 | Case 2
 | A | 1.167
 | B | 3.4532
 | Seal Retaining Ring
 | A |  | 0.9943
 | Case 1
 | A
 | B
 | C
 | D

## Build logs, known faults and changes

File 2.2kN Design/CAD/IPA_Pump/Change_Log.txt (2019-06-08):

04/17/2019
Change Log: EFS-100-041619 to EFS-100-041719

-Impeller face: In leu of vane fillets, vertex of impeller eye must be brought down to run parallel to internal flat of pump chamber (on case 2)

-Impeller Length: Impeller lenghth extended both at step and coupler end to match machined dimensions

-Case 1: Impeller bore on front face opened up ~0.02 in for rotational clearance (Ref: Handbook of Turbomachinery - Earl Logan)

-Bearing Collar: Impeller step extrusion extended by 0.0268 in to account for location adjustment of impeller inside pump chamber

-Seal retaining ring: added to assembly

-Oring added to assembly (placeholder; not meaasured to rubber rings in shop)

-Materials: Material selections have been added for components that perviously hadn't been assigned

- Shoulder bolts: Accurate length shoulder bolts added (w/ nuts)

- Bearing plate: Counter bore added to account for roller and collar overhang

- Diffuser Flange: Switched bolting pattern to 4 instead of 6

- External References: All external references have been unlinked to avoid assembly issues

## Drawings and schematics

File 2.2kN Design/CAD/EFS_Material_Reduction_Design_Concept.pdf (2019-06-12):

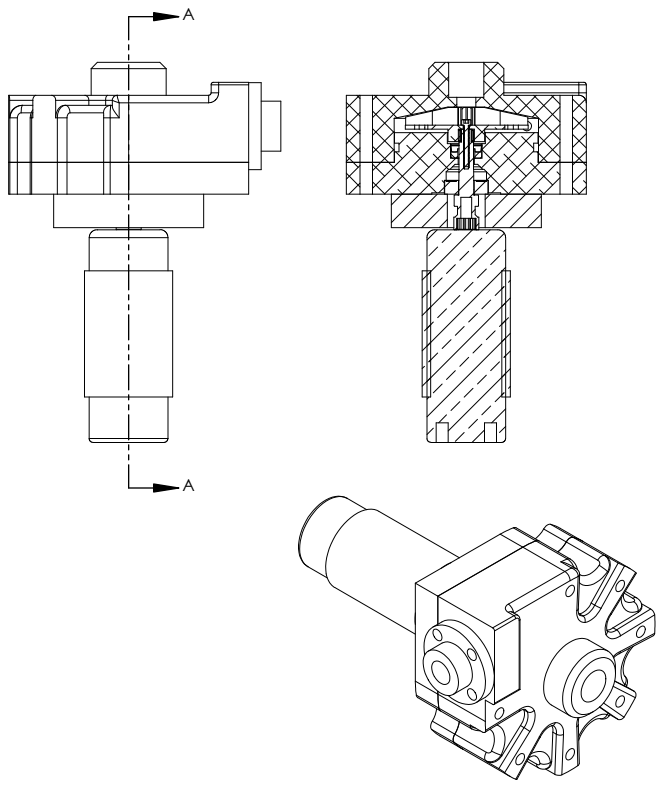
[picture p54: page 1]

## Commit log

2019-06-08 Add files via upload
    Archived files from EFS iteration 2 project work.
    [8mm Bearing SKF 608 (RS 286-7530).SLDPRT, Aquastar T20 Water Cooled.SLDPRT, Bearing_Cover.SLDPRT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]
2019-06-08 Add files via upload
    Files pertaining to EFS Iteration 2 for 2.2kN LV4 design parameters.
    [Dimensions.xlsx, EFS_Design_Calculation_Tool.xlsx, EFS_Shaft_Key_Calculation_Tool.xlsx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]
2019-06-08 Solidworks parts and assemblies for EFS
    Solidworks parts and assemblies for EFS Iteration 2 liquid oxygen and isopropyl alcohol pumps.
    [1_inch_collar.SLDPRT, 90298A550_18-8 STAINLESS STEEL SHOULDER SCREW.SLDPRT, 91251A114_BLACK-OXIDE ALLOY STEEL SOCKET HEAD CAP SCREW.SLDPRT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]
2019-06-08 IPA Pump Solidworks Parts and Assemblies
    [91259A101_ALLOY STEEL SHOULDER SCREW.SLDPRT, 95462A029_GRADE 5 STEEL HEX NUT.SLDPRT, Baseplate.SLDPRT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]
2019-06-08 Cryogenic Pump Test
2019-06-08 Impeller Prototype Images
2019-06-08 IPA Pump Testing Media
2019-06-08 Design Concept for Further Impeller Development
    Design Concept for Further Impeller Development. Rear face of impeller features shallow Barske vanes that match the pattern of front vanes of the manufactured impeller. Helps to reduce pressure exper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
    [Impeller_Concept_Backpressure_Barske.SLDPRT]
2019-06-08 Thermal Analysis Photos
    Images from thermal analysis testing of EFS motor and ESC
2019-06-08 Research Documents and EFS Development Resources
    [Capstone Materials Analysis.xlsx]
2019-06-08 Course-Related Material from EFS Capstone
    [Capstone Gantt_.xlsx, EFS ME411 Power Runs.xlsx, EFS ME411 RPM vs Power.xlsx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]
2019-06-08 UTEAP files for EFS Iteration 2
    [Electric Feed System OSGC Purchase Requests.xlsx]
2019-06-12 Future concept for flight-ready weight reduction
    NOTE: This is a rough concept ONLY. Design idea for material reduction and overall simplification for next generation of the PSAS electric feed system. Driving the impeller directly from an extended 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
2019-06-13 Rename 2.2kN Design/Analysis/It2_Impeller_Shaft_Combined_NoFillets.x_t to 2.2kN Design/Analysis/CFD/It2_Impeller_Shaft_Combined_NoFillets.x_t
    [It2_Impeller_Shaft_Combined_NoFillets.x_t]
2019-06-13 Pump volute CFD simulation for StarCCM+
